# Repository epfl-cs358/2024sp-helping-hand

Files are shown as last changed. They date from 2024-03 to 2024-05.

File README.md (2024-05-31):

# Helping Hand

**Beyond Accessibility: Unleashing the Potential of Home Automation to Foster Independence and Inclusivity for Individuals with Unique Needs**

2024 - EPFL (CS-358) MIT - Group project



## Project's Overview

Helping Hand is an innovative project designed to enhance the independence of individuals with **mobility impairments** through adaptable **home automation**.
The core of the project is a **modular box** equipped with a **Wi-Fi** enabled microcontroller and a plotter like mechanism that allows **remote control** of various **household appliances**.
This system can be operated via a **smartphone or WEB application**, making it accessible for users with limited physical capabilities.

Inspired by the needs of Sean, a person with ALS who has limited mobility, Helping Hand aims to facilitate tasks such as opening doors and operating blinds without assistance.
The modular box can accommodate different remote controls, allowing users to control multiple devices through a single, user-friendly interface.
The project prioritizes accessibility, ease of use, and adaptability, making it a versatile solution for various remote-controlled appliances.

**Note**: you can check out the original project's proposal: [Helping Hand project proposal](proposal/out/proposal.pdf).

## Project's Structure

Below is a brief explanation of this repository's structure to provide context and aid readers' comprehension in the following sections of this document.

- `code` directory: contains all the code for the different parts of the project.
    - `CVserver`: the python server side program responsible for image processing and remote buttons automatic detection and configuration.
    - `esp32-cam`: the ESP-32 Cam [Arduino](https://www.arduino.cc/) code to be able to capture an image using an HTTP request.
    - `esp32-controller`: the ESP-32 C6 code that is responsible to control the motors and press the remote's buttons on the main plate.
    - `helping_hand`: the [Flutter](https://flutter.dev/) code used to create the application from which we control the device and interact with the different microcontrollers in the system.
- `design` directory: contains all the 3D modeling files and exports along with the laser cut sheets.
- `diagrams` directory: contains all the protocol diagrams specifying how the different parts of the system interact with one another.
- `documentation` directory: contains all the pictures and schematics to be able to reproduce this project.
- `proposal` directory: the [LaTeX](https://www.latex-project.org/) document used to write the original project proposal.
- `reports` directory: our first meetings reports to agree on what to do together.

## Build It Yourself !

This section is all about providing instructions and material to be able for anyone to reproduce this project by themselves.

### Hardware

This project is mainly composed of electronic components, laser cut _4mm_ MDF plates and 3D printed parts.

#### Main body

Here are the steps to follow to build the main body (and the camera module) of the system:

1. Laser cut the following MDF (4mm) parts
    - [Plotter](design/plotter/plotter.dxf)
    - [Cam holder](design/camholder.dxf)
2. 3D print the required parts (PETG)
    - [Gear holders for the column: top](design/plotter/plotter_column_2_belt_holder_top.stl)
    - [Gear holders for the column: bottom](design/plotter/plotter_column_2_belt_holder_bottom.stl) 
    - [All clamp parts](design/clamp/)
    - [All y axis parts](design/y_axis/)
3. For the assembly you will also need the following parts:
    - One _8mm_ diameter stainless steel bar, _290mm_ of length
    - One _8mm_ diameter stainless steel bar, _305mm_ of length
    - Two _8mm_ diameter stainless steel bar, _160mm_ of length
    - Four _8mm_ rod bearings to slide on the bars
    - Two _5mm_ diameter stainless steel bars, _150mm_ of length
    - Four _M4_ screws with nuts (two are nylon insert lock nuts), _35mm_ of length
    - Four _M4_ screws with nuts, _12mm_ of length
    - Eight _M3_ screws with nuts, _10mm_ of length
    - One _M5_ screw with nut, _20mm_ of length
    - Two _M5_ screws with nuts and spacers, _20mm_ of length
    - Eight _M3_ screws, _12mm_ of length
    - Two _M2.5_ screws with nuts, _12mm_ of length
    - Eight neodymium magnets, cubes of _5mm_ sides
    - Two rubber sheets, _30mm_ by _12mm_
    - Two plastic belts, _610mm_ and _320mm_
    - End gears and axes for the connection between belt and motors
4. Assemble everything and glue the MDF parts as indicated in the 3D step file: [Full assembly .step file](design/assembly.step).

For reference, here are some pictures of the full result assembly:

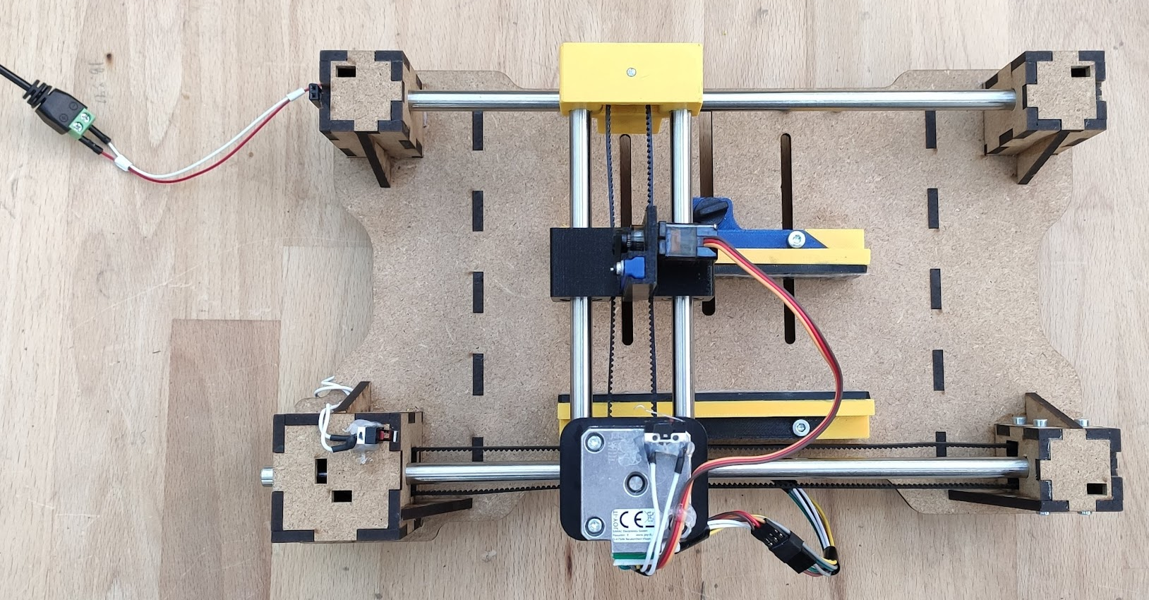
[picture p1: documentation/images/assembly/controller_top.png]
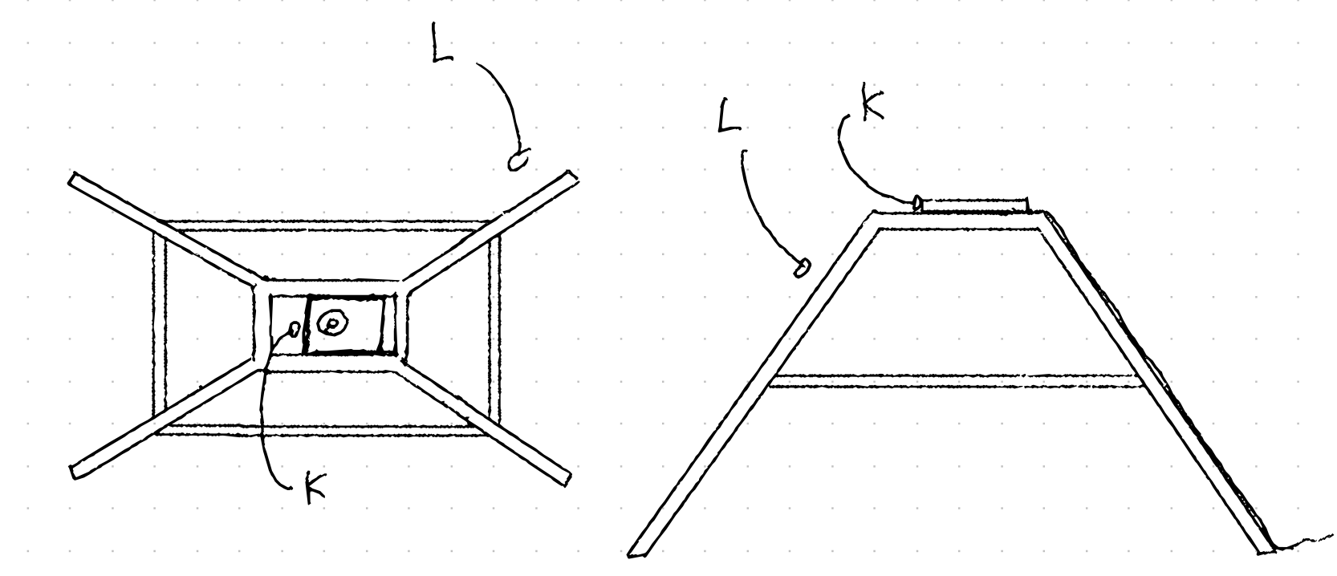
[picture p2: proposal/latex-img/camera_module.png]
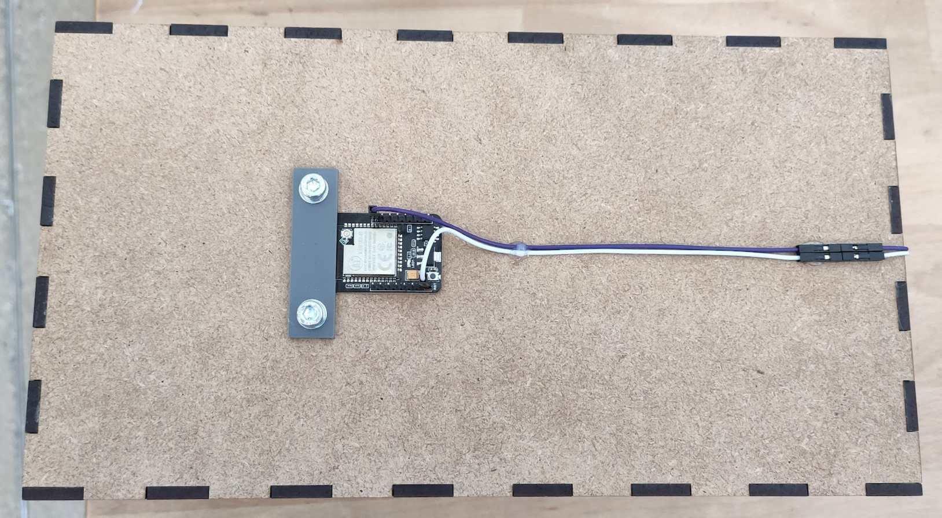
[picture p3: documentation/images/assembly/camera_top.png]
      

#### Electronics

Here are all the required electronic components:

- ESP-32 CAM
- ESP-32 C6
- Stepper mottors Nema14-01 (2 times)
- Motors drivers A4988 (2 times)
- Servo motor MG90S
- DC to DC converters (2 times)
- Two limit switches
- Condensator _100uF_ (2 times)
- Power Supply 9V

Wire everything together as indicated in the following schematic:

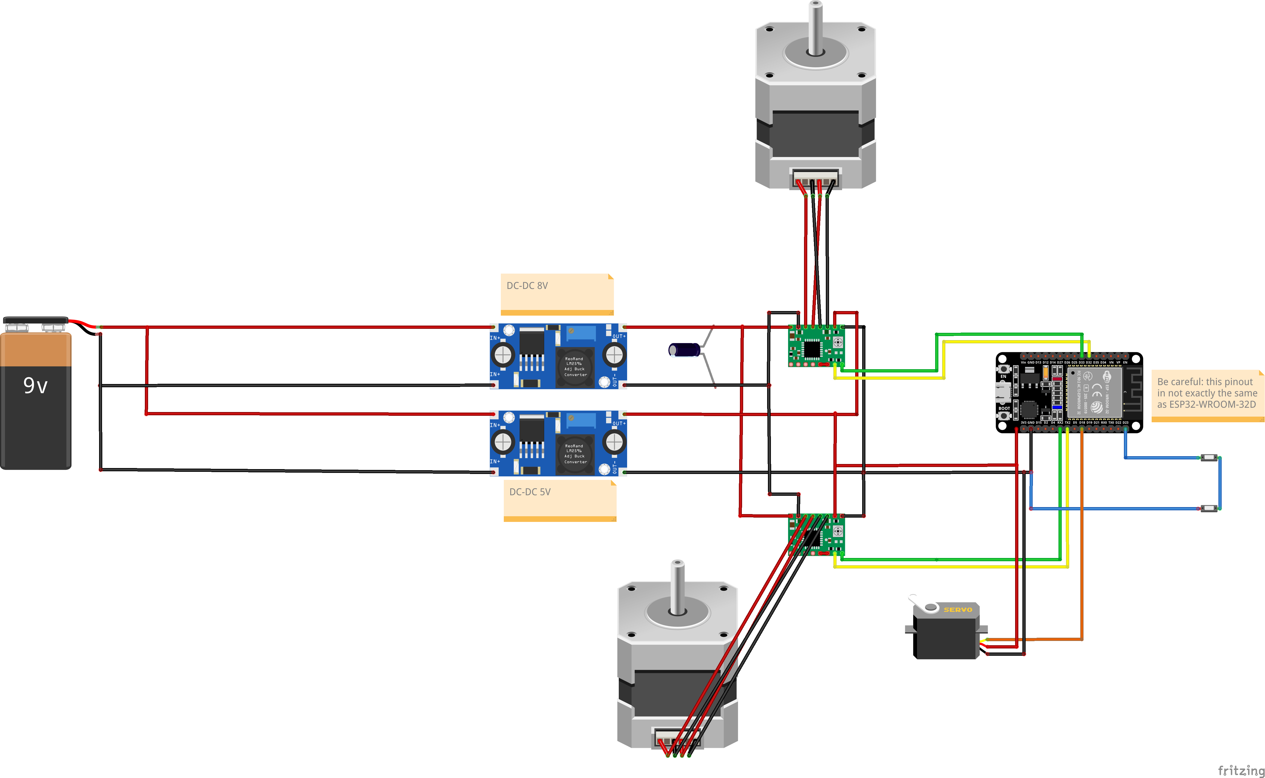
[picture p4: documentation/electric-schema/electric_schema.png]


**Note**: make sure to leave some length on the cables used on the travelling parts.

For reference, here are some pictures of the resulting cable management (done under the board):

<br>


### Software

We have four system components that need to interact with eachother in order to function properly.
The following diagram summarizes the different intractions between the components:

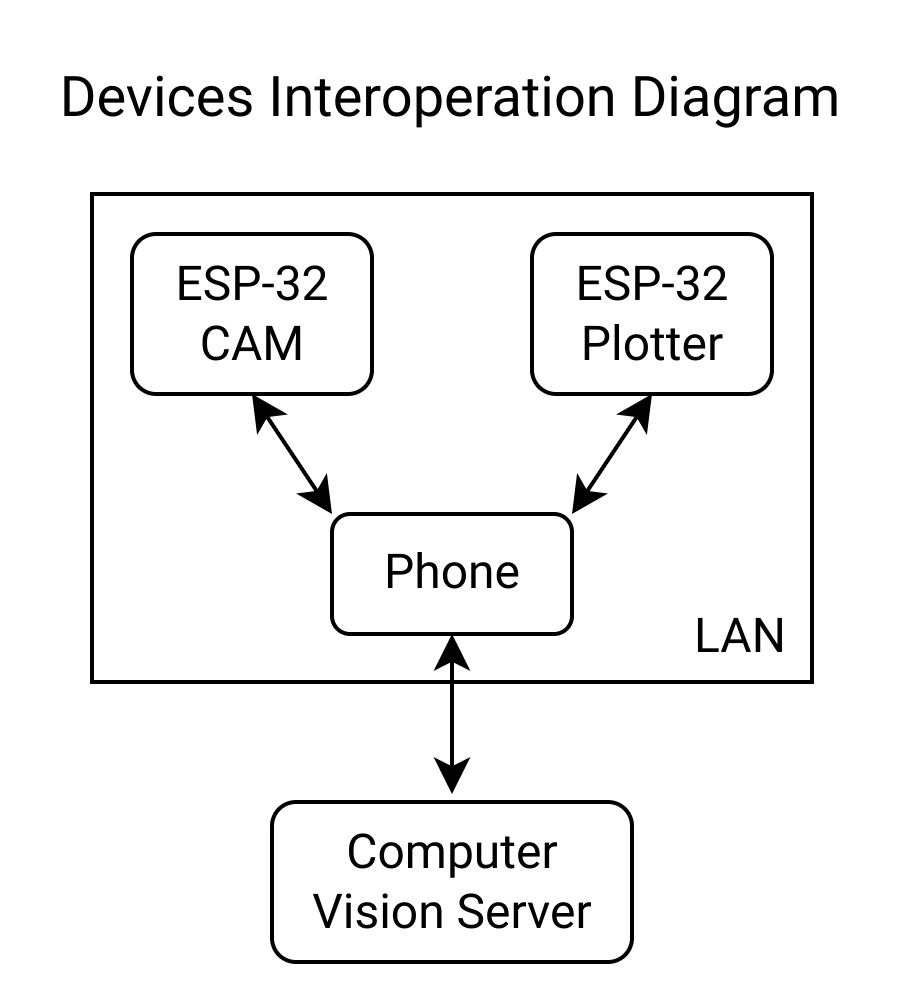
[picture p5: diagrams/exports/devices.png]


#### Application

All the system is driven by a [Flutter](https://flutter.dev/) cross-platform application.

You can install the Flutter dev environment by following the installation instructions (on any OS): https://docs.flutter.dev/get-started/install.

Then navigate to the directory of the application, `code/helping_hand`.
You can now launch the application on your platform of choice, on web for example `flutter run -d chrome`.
To build for other targets, you can follow the standard Flutter building procedures: https://docs.flutter.dev/deployment.

Here are a few pictures of the application interface:

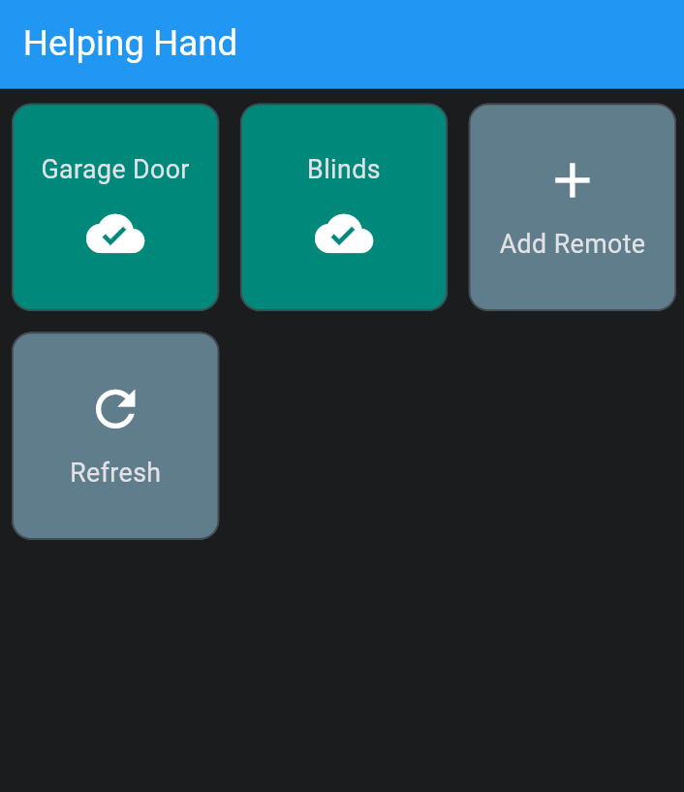
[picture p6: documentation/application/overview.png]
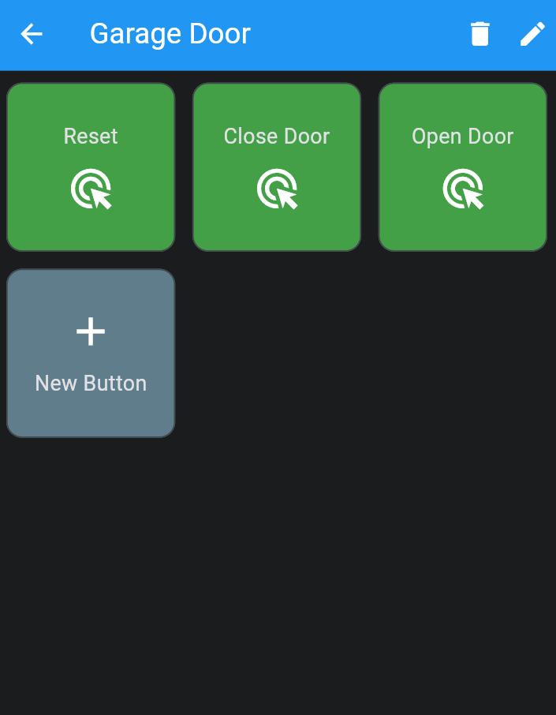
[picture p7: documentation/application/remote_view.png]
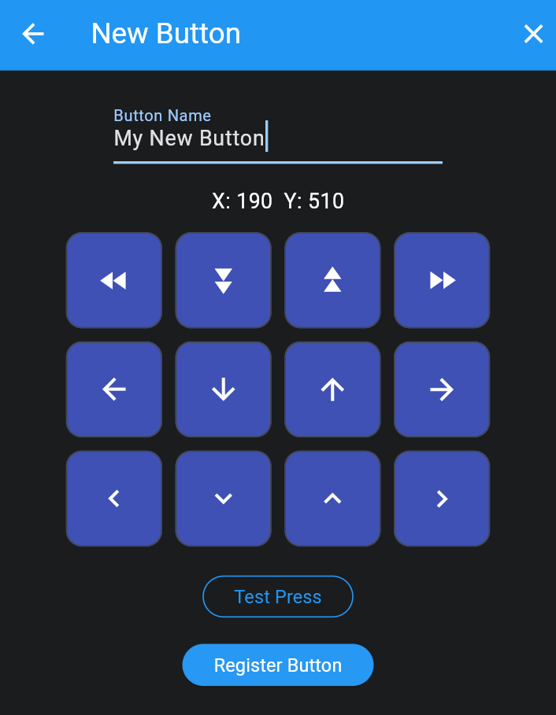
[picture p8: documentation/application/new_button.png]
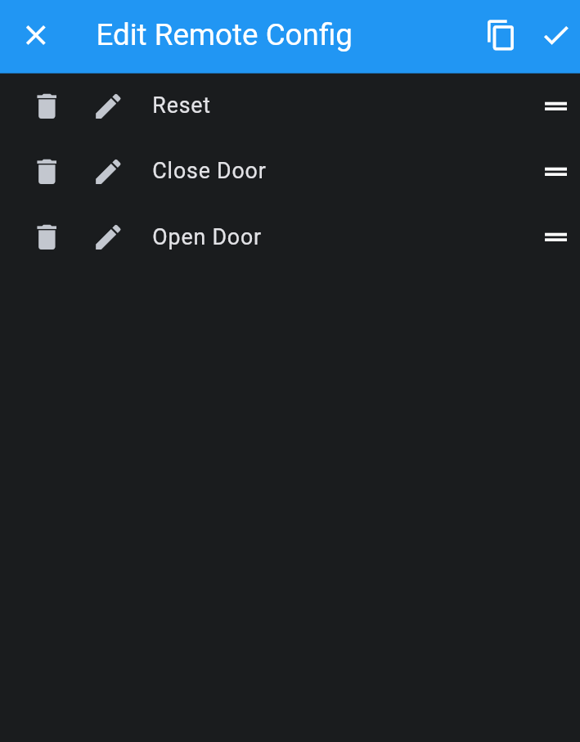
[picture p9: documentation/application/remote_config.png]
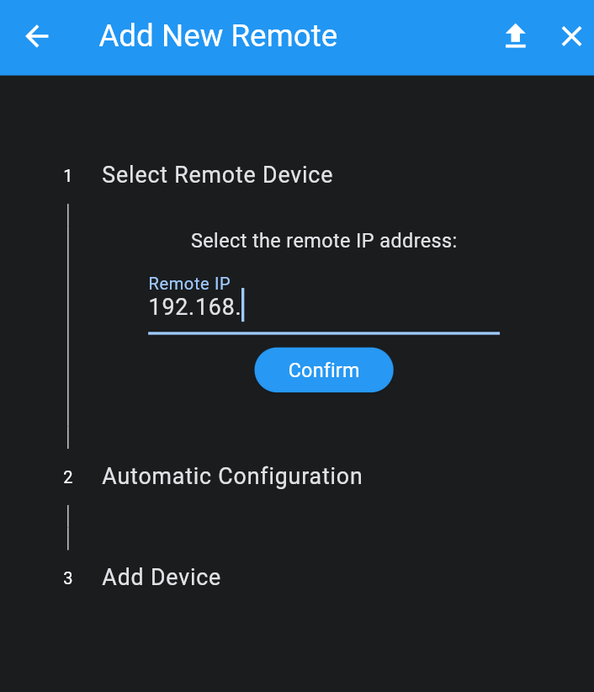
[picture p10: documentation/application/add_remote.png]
    

#### Arduino

We use the [Arduino IDE](https://www.arduino.cc/en/software) to flash the two ESP-32 boards:

- **ESP-32 Cam** (the automatic configuration module using the camera): flash the `code/esp32-cam/esp32-cam.ino`. For more information about this module, please refer to the [ESP-32 CAM README](code/esp32-cam/README.md).
- **ESP-32 Plotter** (the remote controller): flash the `code/esp32-controller/sketch_webServer/sketch_webServer.ino`. For more information about this module, please refer to the [ESP-32 C6 README](code/esp32-controller/README.md).

#### Computer Vision Server

We used a [Python](https://www.python.org/) web server (running on any computer or in the cloud) powered by the [Flask](https://flask.palletsprojects.com/en/3.0.x/) framework.

Refer to the associated README to setup the python server: [Python CVserver Setup README](code/CVserver/README.md).

## Contributors

- Yoan Giovannini ([@unglazedstamp](https://github.com/unglazedstamp))
- Nour Guermazi ([@nourguermazi](https://github.com/nourguermazi))
- Lucas Jung ([@gruvw](https://github.com/gruvw))
- Pinar Oray ([@pinar-oray](https://github.com/pinar-oray))
- Jonas Sulzer ([@violoncelloCH](https://github.com/violoncelloCH))

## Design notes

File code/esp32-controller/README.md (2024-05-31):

# Motor controller software
This folder contains the code running on the ESP-32-C6 which controls the motors.

## Setup to work with the ESP32-C6

### Arduino IDE
You first have to flash the sketch_initMemory.ino with your wifi credentials in the code (only the first time), then you can flash the sketch_webServer.ino code which will connect to the wifi to control the motors.

At the beginning of the file you will find all the constants needed to change the behavior of the helping-hand: the motors max speed, calibration speed, the pins number on the board and others.

### Wiring
wiring schema of the ESP32-C6
Connect all the wiring according the the schema and then adjust the pins to your ESP board and in the program.

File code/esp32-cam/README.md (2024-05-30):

# Camera module software
> This folder contains the code running on the camera module, an ESP32-CAM module. It has `/capture` endpoint serving an image of the remote.

## Setup to work with the ESP32-CAM

### Arduino IDE
> To work with this existing project, open the esp32-cam.ino file with Arduino IDE.

1. In `File>Preferences` in the field `Additional boards manager URLs` add the following two lines:
```
https://arduino.esp8266.com/stable/package_esp8266com_index.json
https://raw.githubusercontent.com/espressif/arduino-esp32/gh-pages/package_esp32_index.json
```
2. In `Tools>Board>Boards Manager` install the `esp32` package.
3. In `Tools>Board>esp32` select `AI Thinker ESP32-CAM`
4. For the Serial connection, set the baud to `115200` (dropdown at the top right of the serial console).

#### Setting the WIFI credentials
The WIFI credentials (SSID and Password) are set in the main Arduino project file: `esp32-cam.ino`. At the top of the file (line ~35) the credentials have to be set in the following lines:
```
// ===========================
// Enter your WiFi credentials
// ===========================
const char* ssid = "wifi-ssid";
const char* password = "wifi-password";
```

#### Flashing
`GND` and `IO0` need to be connected while powering on the ESP for it to boot in flashable mode. Use a cable to connect them. To boot the flashed program, remove the cable and reboot (i.e. power cycle) the ESP with the two pins not connected.

### Wiring
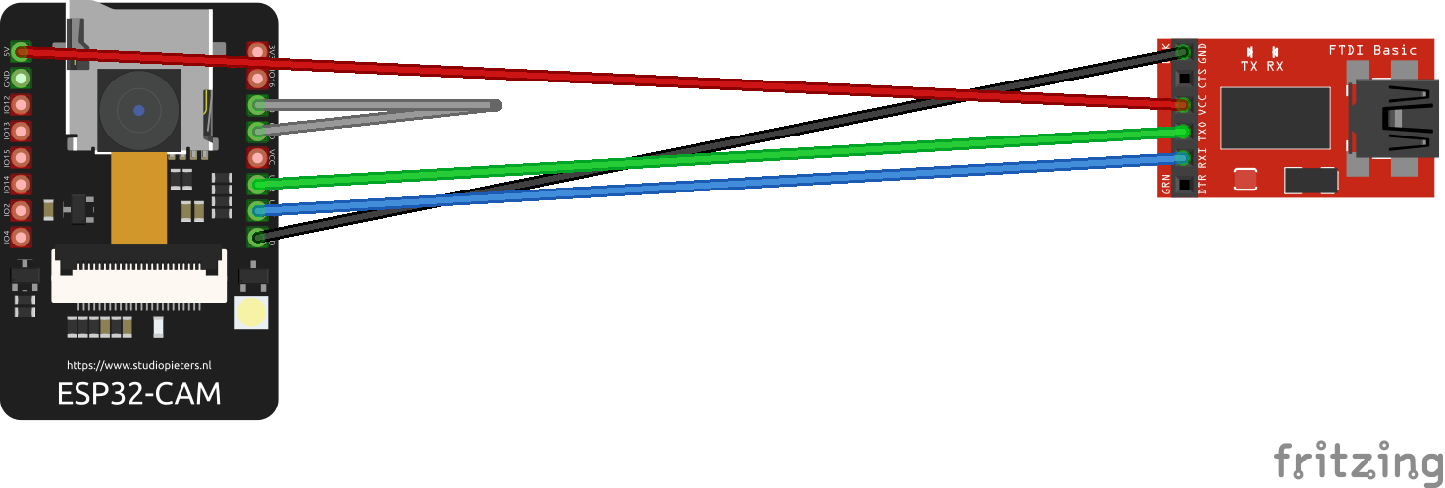
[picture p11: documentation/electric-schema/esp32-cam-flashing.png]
wiring schema for flashing

as described in the Course Handbook in Chapter 25.4  
note the two pins that need to be bridged (only) during flashing

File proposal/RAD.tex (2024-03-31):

\section{Risk Assessment}

In this section, we conduct a comprehensive risk assessment to identify potential challenges and vulnerabilities that could impede the success of our project.
By evaluating technological risks we aim to proactively address these issues through strategic planning and prototype development.
This assessment underscores our commitment to ensure the resilience and adaptability of our project, thereby minimizing the likelihood of failure and maximizing its overall effectiveness.

% reword the below p
%  remote adaptability: required pressure for each remote is different: some hard-pressed, some don't require as much pressure to acknowledge a button press. another problem is that the remote sizes
%                         vary a lot in length but especially in width, which makes designing and creating a clamp that fixes most of the remotes difficult.  
%  calibration: the calibration as a first step is to be done manually, which would include manually moving the pushing mechanism to the button via the phone application and setting it up as a button. This might be somewhat 
%                 time consuming and hard to configure for non-technical users. 
%                 The next step to the setup includes computer vision.
%                 This also comes with its own challenges, and is complex because of the camera quality of the ESP32-CAM, the nature of remotes and the setup restrictions: small and non-tv remotes are likely to have similar colored buttons to 
%                 the remote's main body, and this makes recognition of individual buttons difficult. Another issue is that the setup, i.e. placing the remote in the clamp is done by a person, and this causes reliability issues
%                 in the sense that not everyone can place and clamp the remote perfectly, and this will cause a sligtly different placement each time. This will cause in a different lightning and a different angle of view for
%                 the camera to pick up. This might affect the accuracy of the image recognition. The computer vision part requires an external computer to set up button positions, and this information is then
%                 sent to the phone application, Here, the communication between the computer, the phone app and the plotter is crucial and complicated. 

\begin{itemize}
    \item Power supplies to steppers:\\
        As mentioned in the manual, inadequate wiring practices and carelessness may lead to frying a computer or damaging the parts, especially the motor drivers and the stepper motors, potentially putting at risk the functionality of the project.
    \item Control of the solenoid:\\
        While the solenoid allows for a completely vertical and uni-directional movement, since we don't have experience with them, we're not sure how precisely we can control the acceleration and force of the resulting movement.
        An alternative could be to use a stepper motor instead for pressing the remote buttons.\\
        An additional risk could be that not all buttons require the same pressure. It could be difficult to adapt to this.
    \item Adaptability to different remotes:\\
        The project's adaptability to different remote controls is a challenge, as compatibility issues may arise with various types of remotes due to the vast spectrum of sizes. The amount of different size and shapes possible makes it complicated to design the clamp mechanism. 
    \item Magnet interferences:\\
        The presence of magnets in the project could disrupt the operation of sensitive electronic components such as the solenoid push-down mechanism, motors or the WiFi chip of the ESP32, leading to unpredictable behavior.
    \item WiFi network stability:\\
        The reliance on WiFi connectivity on those ESP32 microcontrollers introduces a risk related to network instability, which could affect communication between project components.
    \item Ease of configuration:\\
        The configuration and calibration of the plotter will have the possibility to be done in two ways: manually via the phone app or with computer vision via a computer. The manual setup may be time consuming for remotes with many buttons. 
        The camera and computer vision setup may be hard to configure for non-technical users. This option also has its own additional challenges. The recogni̇ti̇on of the remote and its buttons rely on the camera, the placement of the remote, the lightning of the room
        and overall restrictions due to remote design. These may affect the accuracy of the image recognition.
    \item Computer vision to button press precision:\\
        Detecting the correct position and therefore being able to guarantee a precise button press while using computer vision to calibrate and configure the device could be difficult for the same reasons listed in above point.
\end{itemize}

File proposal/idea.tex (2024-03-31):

\begin{minipage}[t]{0.65\textwidth}
    In the depicted image, you'll find Sean and Lucas.
    Sean, a colleague of Lucas' mother, is unfortunately grappling with \href{https://en.wikipedia.org/wiki/ALS}{amyotrophic lateral sclerosis}\footnotemark (ALS), a terminal neurodegenerative disease that progressively diminishes his mobility.
    Presently, he has to spend his days in an electric wheelchair, with only partial movement in his wrists.
    As a result, he relies on others for even the most basic tasks, such as opening a door or operating the lights in his home.
    Despite these challenges, Sean can still manage his smartphone while in his chair, thanks to a specialized joystick and a button.
    The objective of this project is to develop an adaptable solution that empowers people in a similar situation to regain some independence through the use of certain appliances in their home.
\end{minipage}\hfill
\begin{minipage}[t]{0.30\textwidth}
  \centering\raisebox{\dimexpr \topskip-\height}{
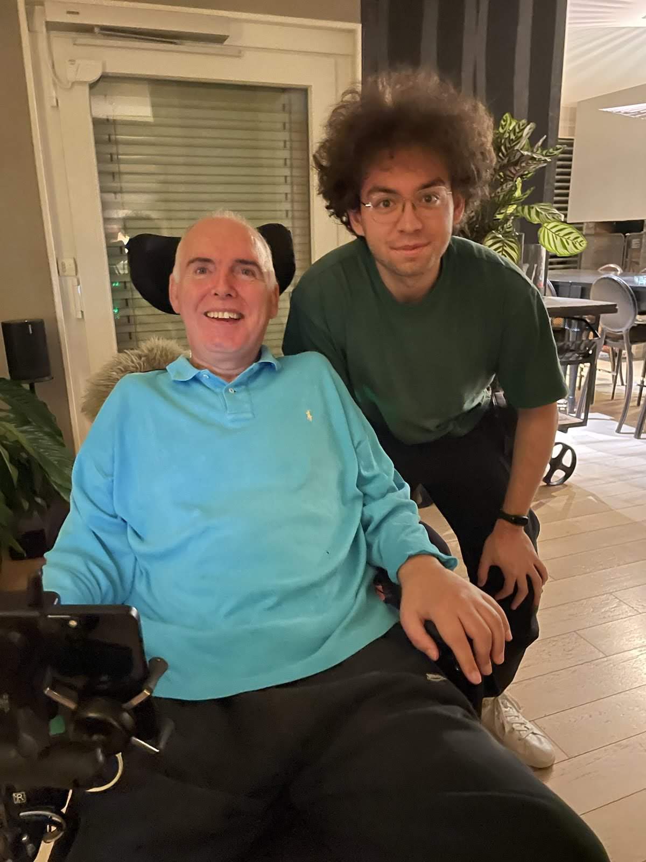
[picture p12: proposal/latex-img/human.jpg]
  }
\end{minipage}
\footnotetext{Amyotrophic Lateral Sclerosis: \url{https://en.wikipedia.org/wiki/ALS}}

\vspace{-10pt}

\section{High-level description}

The project aims to create a box in which the user can install any one of the various remote controls they have in their home.
The box will be equipped with a \footlink{plotter}{https://en.wikipedia.org/wiki/Plotter} like mechanism and a Wi-Fi capable microcontroller, allowing for remote operation of the enclosed remote control by having a solenoid activator attached to the plotter press on the buttons.
The box must be designed in such a way that the buttons are still usable without causing disruption to a user who prefers direct manual control of the remote.
The design of the case should also be easily adaptable to different type of remote controls.

Even though in the scope of the project we'll only be able to build one box, the idea is that a user can install multiple of these boxes for as many remotes as they want to use.
Each box is connected to the Wi-Fi network of the home it is installed in, and the user can command it by using an application on their smartphone.
Naturally, the application will be meticulously designed to maximize \footlink{accessibility}{https://en.wikipedia.org/wiki/Accessibility} for users with limited input capabilities.
Collaborative feedback and discussions with Sean will play a pivotal role in enhancing the system's accessibility, as he provides valuable insights from the perspective of a user with disabilities.

This project idea will be applied to some of the remote controlled appliances in Sean's home, notably in the two following use cases:
\begin{enumerate}
    \item In his residence, Sean has installed a motorized door (as seen behind us on the picture) that can be operated with a button press using a dedicated remote control, on which we could install the system.
        This holds significant importance for the project, as it would enable Sean to independently access his terrace and garden without relying on someone else to open the door for him.
    \item Additionally, he possesses remote-controlled blinds that he wishes to manage through his smartphone.
        This functionality would empower him to effortlessly close the blinds while working on his computer when the sun begins to shine through his window, or before going to bed.
\end{enumerate}

This project maintains its independence from specific use cases at Sean's place, aiming to be easily adaptable to most remote controls.
Nevertheless, establishing a direct connection and receiving periodic feedback from an end user like Sean during development significantly contributes to ensuring the system's accuracy and user-friendliness directly from the targeted audience.

Furthermore, the potential extends beyond Sean's specific needs: this system could serve as a prototype or a \footlink{minimal viable product}{https://en.wikipedia.org/wiki/Minimum_viable_product} (MVP)/pilot experiment for a cost-effective and easy to install commercial solution for a future startup company.
Such a solution would offer increased autonomy to numerous individuals in their daily lives.
It would be particularly competitive compared to existing alternatives that are very costly and often necessitate replacing the entire system with a ``smart``/digital version even though the one currently in place still works properly.
In fact, even though this system is targeted at people with disabilities, it might also come in handy for everyone who wishes to have access to their regular appliances through a common, digitalized interface.

A fundamental aspect of this project is its commitment to adhering to \footlink{open standards}{https://en.wikipedia.org/wiki/Open_standard} and the \footlink{open source}{https://en.wikipedia.org/wiki/Open_source} philosophy.
This commitment ensures the system's ease of customization for anyone interested in enhancing, tweaking, or adding functionalities.
This stands in stark contrast to existing solutions in the market, which are often characterized by closed systems that are challenging or even impossible to integrate into a accessible and simple to use central app and lack customization options.

\subsection{User Stories}

\begin{itemize}
    \item As a user with limited mobility, I want to independently open and close my motorized door using my smartphone, so I can access my terrace and garden without assistance.
    \item As a user who values autonomy, I want the modular box to be connected to the Wi-Fi network in my home, allowing me to control appliances remotely through my smartphone from anywhere in the house.
    \item As a user with a chronic degenerative disease affecting my mobility, I want to control my remote-controlled blinds via a smartphone app, allowing me to manage sunlight in my room without relying on others.
    \item As a user with unique needs, I want the modular box to be adaptable to different types of remote controls in my home, ensuring flexibility in controlling various appliances.
    \item As a potential end user looking for cost-effective solutions, I am looking for a commercial solution that offers increased autonomy, making it a viable and affordable option for individuals with diverse needs.
    \item As a developer or tech enthusiast, I want the system to adhere to open standards and open source philosophy, enabling me to enhance, customize, or add functionalities by making \footlink{pull requests}{https://en.wikipedia.org/wiki/Distributed_version_control} to the project's repository.
    \item As a user assisting someone with unique needs, I want the setup of the box and the configuration of the app to be straightforward and require minimal technical expertise, ensuring that I can provide support without complications even if I am not very skilled with new technologies.
    \item As a user with limited physical dexterity, I want to operate my TV remote control from my smartphone using the modular box system, allowing me to enjoy television without struggling with a conventional remote control.
\end{itemize}

\subsection{Existing Projects}

After searching online for existing solutions, Lucas discovered that none fully align with the objectives outlined above.
Many of the identified projects focus on complete replacement of the remote control, utilizing new emitters controlled by a microcontroller.
These implementations typically involve either \footlink{infrared emitters (project)}{https://github.com/computerjazz/ir-mobile} that record signals from the targeted remote control or \footlink{radio frequency (project)}{https://github.com/loopj/open-rts} based emitters that analyze the \footlink{rolling codes}{https://en.wikipedia.org/wiki/Rolling_code} of the initial device.

While these approaches are great and offer reliable performance, they are not well-suited for the inclusive and versatile goals of this project.
They often require installation on specific hardware and involve intricate setup and code manipulation to function.
This project aims to take a more broad and user-friendly approach by designing an adaptive solution that seamlessly integrates with various remote controls out of the box, whatever transmission mechanism they might use.

\section{Technical Specifications}

\textbf{Hardware Components}

The core of the modular box will utilize the \footlink{ESP32}{https://www.espressif.com/sites/default/files/documentation/esp32_datasheet_en.pdf} microcontroller for its compact size, low power consumption, and Wi-Fi capabilities.
This will enable seamless communication with the home network and the user's smartphone application.
Each box will be equipped with one ESP32 that will host and expose a \footlink{Web API}{https://en.wikipedia.org/wiki/Web_API} to interact with the plotter stepper motors and solenoid actuator from the smartphone application via the home Wi-Fi network.

The remote control will be housed in a laser-cut adjustable wood case/holding to accommodate various sizes and shapes.
The design should prioritize accessibility, ensuring that buttons remain accessible for direct manual control when needed.

Equipped with a plotter-like system, the box will simulate human interaction with the enclosed remote control.
This plotter system enables precise and controlled button presses, ensuring reliable functionality by moving to the exact position of the button and then actuating the button through a purely vertical movement done by the solenoid.

In a basic configuration process, after installing the remote in the box, the user selects button position by manually positioning the plotter using arrow buttons in the app.
The coordinate of that position is then saved and associated with a button and label in the app.

Additionally, to facilitate the setup process, an attachable module with a camera allows to assist the configuration of the device through computer vision.
If a user has multiple boxes in their home, they can use that single camera module to configure all of the boxes since it's only used during the setup process.
The computer vision, running on an external computer, also communicates over the network with the ESP32 board as well as with the camera to get the video feed.
The software detects the buttons on the image of the remote and allows the user to select the buttons to make available through the app.
For each of the chosen buttons, it auto-detects the exact position to execute the button press operation thanks to the visual feedback provided by the camera.
In case the user prefers not to use the camera and computer vision or in case the computer vision fails due to low contrast or a special remote type/design the manual setup process serves as a fallback. 

\begin{minipage}[t]{0.45\textwidth}
    \centering\raisebox{\dimexpr \topskip-\height}{
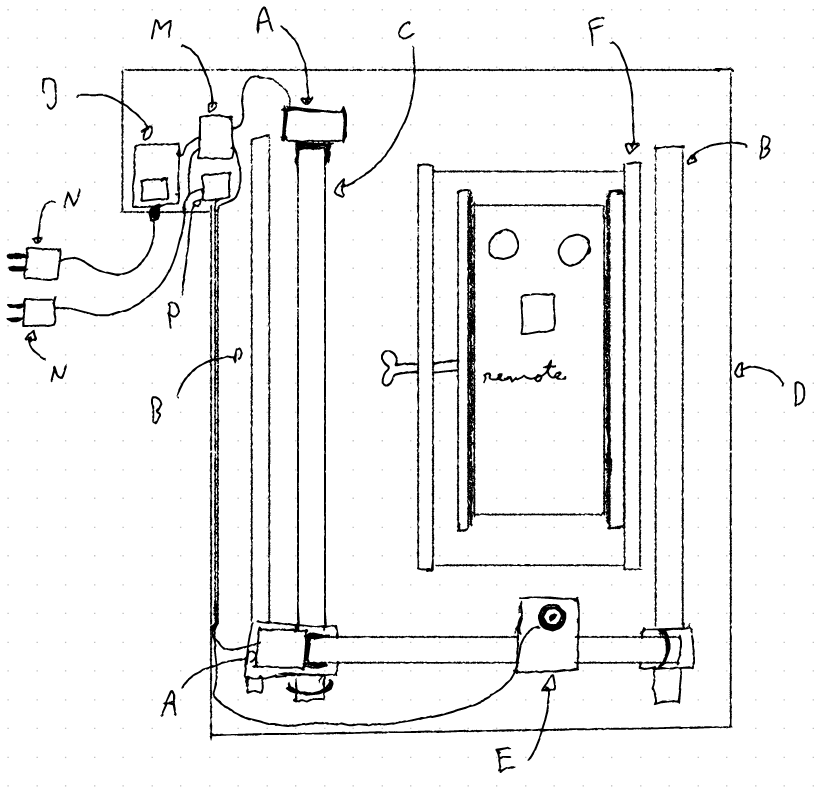
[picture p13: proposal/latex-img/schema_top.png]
    }
\end{minipage}\hfill
\begin{minipage}[t]{0.5\textwidth}
    Looking from the top, we can see the base plate with the different components on it.\\

    Legend:
    \begin{itemize}
        \item (A) motors
        \item (B) rail (metal rod)
        \item (C) lead screw
        \item (D) base plate
        \item (E) solenoid holder
        \item (F) clamp
        \item (G) solenoid
        \item (H) wingnut
        \item (I) rubber
        \item (J) ESP32-c6
    \end{itemize}
\end{minipage}

\begin{minipage}[t]{0.5\textwidth}
    \begin{itemize}
        \item (K) ESP32-CAM
        \item (L) camera module
        \item (M) motor controller
        \item (N) power supply
        \item (P) solenoid controller
    \end{itemize}
    \vspace{5mm}

    From the side we can see how the plotter can move on the two axis hovering above the remote.
\end{minipage}
\begin{minipage}[t]{0.45\textwidth}
    \centering\raisebox{\dimexpr \topskip-\height}{
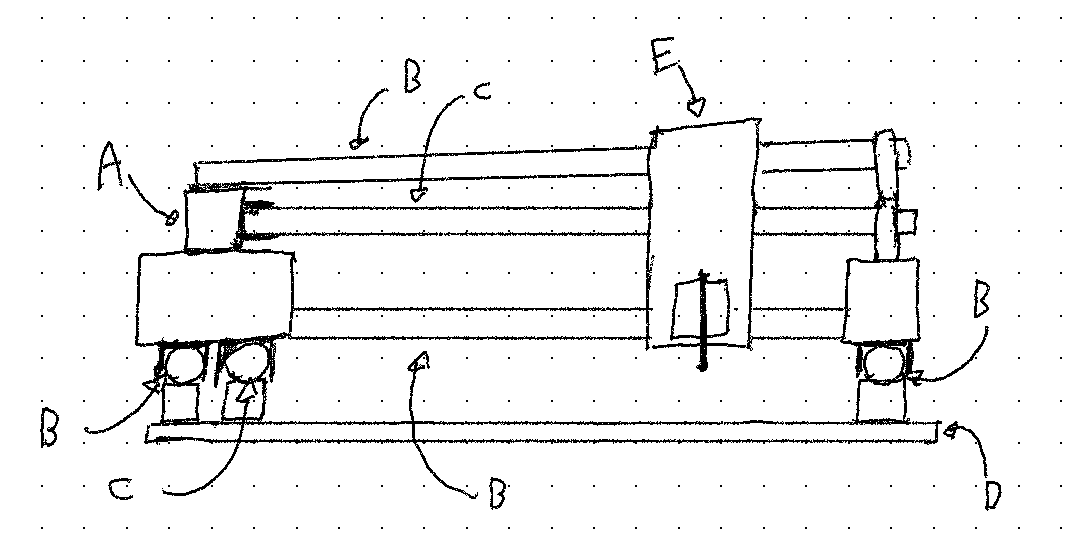
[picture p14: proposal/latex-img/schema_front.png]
    }
\end{minipage}\hfill

\begin{minipage}[t]{0.45\textwidth}
    \centering\raisebox{\dimexpr \topskip-\height}{
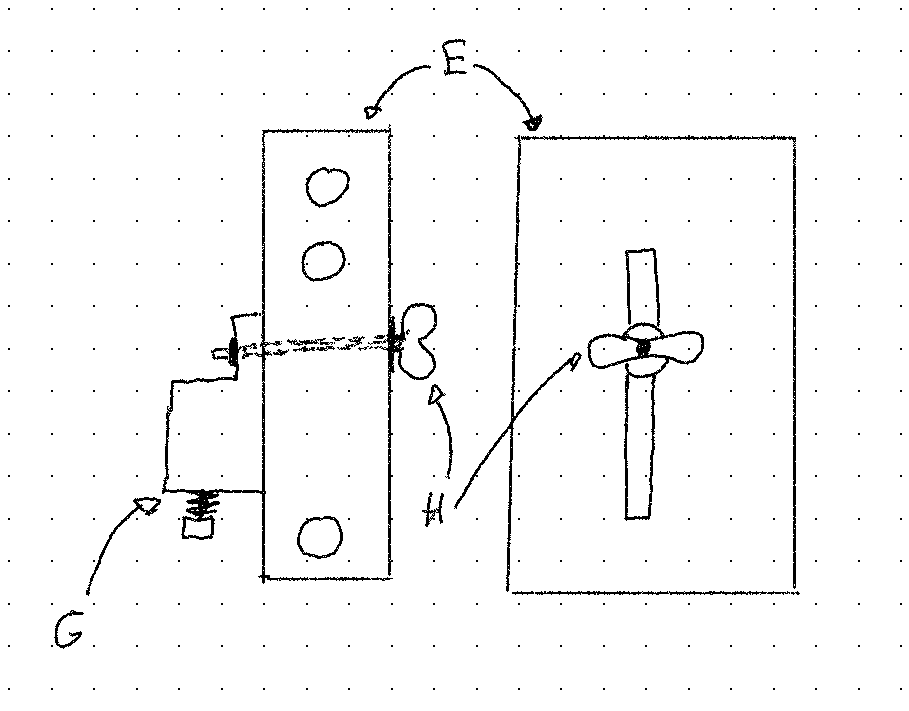
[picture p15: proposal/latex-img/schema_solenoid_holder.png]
    }
\end{minipage}\hfill
\begin{minipage}[t]{0.5\textwidth}
    \vspace{5mm}
    In the detail view of the solenoid holder we can see how the height of the solenoid can be adjusted to match the thickness of the remote.
\end{minipage}

\begin{minipage}[t]{0.5\textwidth}
    \vspace{5mm}
    The clamp allows to safely hold the remote in place.
\end{minipage}
\begin{minipage}[t]{0.45\textwidth}
    \centering\raisebox{\dimexpr \topskip-\height}{
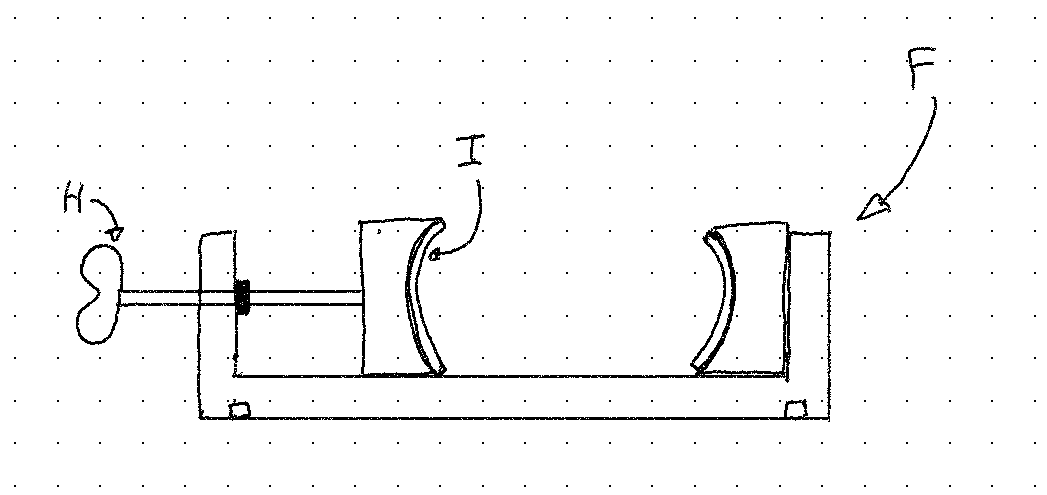
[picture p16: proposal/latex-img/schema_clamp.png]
    }
\end{minipage}\hfill

\begin{minipage}[t]{0.40\textwidth}
    \centering\raisebox{\dimexpr \topskip-\height}{
    }
\end{minipage}\hfill
\begin{minipage}[t]{0.5\textwidth}
    \vspace{5mm}
    And finally the camera module.
\end{minipage}

\textbf{Software}

The software side of the project will be implemented using \footlink{Arduino}{https://www.arduino.cc/} programming to control the ESP32 microcontroller.
Arduino's user-friendly environment allows for efficient development and rapid iteration.

The dedicated smartphone application will be developed using the \footlink{Flutter framework}{https://flutter.dev/}.
The application will prioritize accessibility, offering a user-friendly interface tailored to individuals with limited input capabilities.
It should allow easy control of multiple boxes installed in the house.

The computer vision part is running on a computer assisting the setup. 
The application on the computer tries to recognize buttons on the remote and allows to easily choose the ones that should be accessible in the smartphone app.
When a button is selected, the computer vision calibrates the position for the button press and allows to test whether a button press actually works.
Finally, the configuration can be transferred to the smartphone by temporarily storing it on the ESP32.

We also need to design and implement an automatic network discovery protocol in order to automatically detect available remotes.
As we want to support many remote encasings in a single home network, the protocol has to assure correct communication between all the ESP32 boards and the smartphone application.

If time permits, we could enhance the application by incorporating a built-in voice controlled feature.
This addition would empower users to effortlessly command various devices using their voice, providing a more seamless experience.

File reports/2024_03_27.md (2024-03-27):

# Refined proposal

## Needs to be covered during the meeting

- [ ] Reviewed the proposal, any remark ?
- [ ] Check for precise drawing and skteches
- [ ] Add drawings and descriptions to the proposal
- [ ] Change the RAD with more details
- [ ] Reviewed the final BOM

## Needs to be done before Friday evening

- [ ]

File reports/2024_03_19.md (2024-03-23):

# Refined proposal

## Needs to be covered during the meeting

- [X] Go through the proposal and change what we want
- [X] Add drawings/sketches/computer graphics to the proposal
- [X] Go through the BOM and check it is ok + check links + find missing materials
- [X] Go through the RAD and check it is ok
- [X] Create the work breakdown (backlog) GitHub project, add dependencies
- [X] Discuss any hardward/software addition that we could add if time allows
    - Make it small
    - Make it look beautiful

## To discuss with TAs

- [X] Servo motors
- [X] Ask about feedback and bring it home to try it out
- [X] Review design + magnet vs fit and clip + z axis ideas

- Add an IR sensor + replayer
- Make it small slick and like a product
- Very easy to configure

## What needs to be Done before next Meeting

- [ ] Drawings to include on proposal
- [ ] Add and comment sketches on the proposal
- [X] Improve RAD and BOM

- [X] Add other use casses to the proposal
- [ ] Everyone review and read the full proposal

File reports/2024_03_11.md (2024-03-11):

# First Meeting

2024_03_11 - RLC781

## Discussed during the meeting

- Setup and invite to common project repository on Github
- Setup meeting reports repository
- Setup latex report and compile using the Makefile
- Talked about the design
- Meetings on Tuesdays 8:30 AM till 9:30 AM

## BOM - Bill of Materials

- 10 servo mottors
- 4 esp8266 + 32
- Small neodium magnets
- Ask for rubber like material

## RAD - Risk Assesment Document

- Power supplies to servos
- Adaptability to different remotes
- Magnet interferences
- WiFi network stability
- How deep the motor goes
- Ease of configuration

## Next Meeting

- First write of BOM and RAD
- Feedback on revised proposal
- Split up work

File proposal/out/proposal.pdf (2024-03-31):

CS-358 MIT | Helping Hand

# Helping Hand

### Lucas Jung - IN BA6 324724 Nour Guermazi - SC BA6 314474 Pinar Oray - IN BA6 311543 Jonas Sulzer - IN BA6 325554 Yoan Giovannini - IN BA6 303934

2024 - 03

Beyond Accessibility: Unleashing the Potential of Home Automation to Foster Independence and Inclusivity for Individuals with Unique Needs

## Contents

1 High-level description | 2
2 Technical Specifications | 4
3 Bill of Materials | 7
4 Risk Assessment | 8

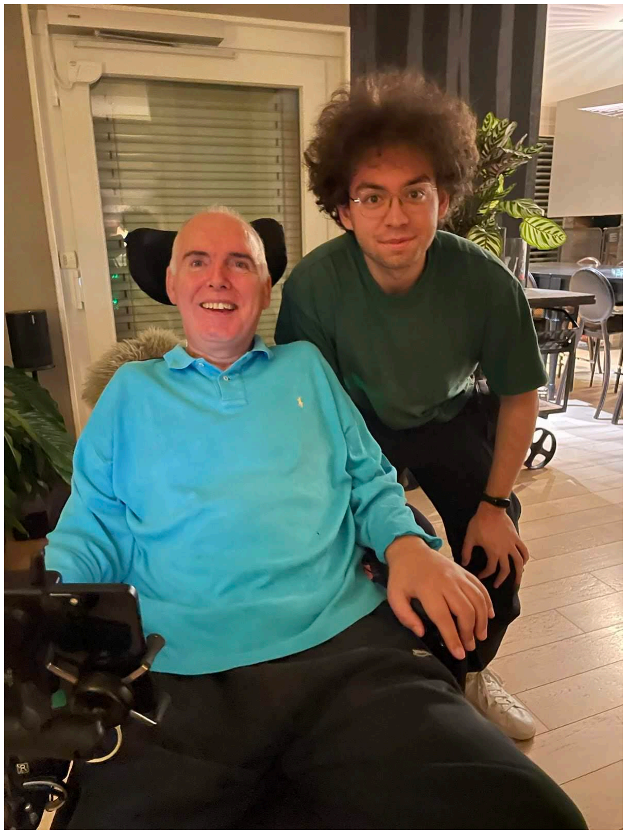
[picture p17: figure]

In the depicted image, you’ll find Sean and Lucas. Sean, a colleague of Lucas’ mother, is unfortunately grappling with amyotrophic lateral sclerosis¹ (https://en.wikipedia.org/wiki/ALS)
(ALS), a terminal neurodegenerative disease that progressively diminishes his mobility. Presently, he has to spend his days in an electric wheelchair, with only partial movement in his wrists. As a result, he relies on others for even the most basic tasks, such as opening a door or operating the lights in his home. Despite these challenges, Sean can still manage his smartphone while in his chair, thanks to a specialized joystick and a button. The objective of this project is to develop an adaptable solution that empowers people in a similar situation to regain some independence through the use of certain appliances in their home.

1Amyotrophic Lateral Sclerosis: https://en.wikipedia.org/wiki/ALS

## 1 High-level description

The project aims to create a box in which the user can install any one of the various remote controls they have in their home. The box will be equipped with a plotter² (https://en.wikipedia.org/wiki/Plotter)
like mechanism and
a Wi-Fi capable microcontroller, allowing for remote operation of the enclosed remote control by having a solenoid activator attached to the plotter press on the buttons. The box must be designed in such a way that the buttons are still usable without causing disruption to a user who prefers direct manual control of the remote. The design of the case should also be easily adaptable to different type of remote controls.

Even though in the scope of the project we’ll only be able to build one box, the idea is that a user can install multiple of these boxes for as many remotes as they want to use. Each box is connected to the Wi-Fi network of the home it is installed in, and the user can command it by using an application on their smartphone. Naturally, the application will be meticulously designed to maximize accessibility³ (https://en.wikipedia.org/wiki/Accessibility)
for users with limited input capabilities. Collaborative feedback and discussions with Sean will play a pivotal role in enhancing the system’s accessibility, as he provides valuable insights from the perspective of a user with disabilities.

This project idea will be applied to some of the remote controlled appliances in Sean’s home, notably in the two following use cases:

1. In his residence, Sean has installed a motorized door (as seen behind us on the picture) that can be operated with a button press using a dedicated remote control, on which we could install the system. This holds significant importance for the project, as it would enable Sean to independently access his terrace and garden without relying on someone else to open the door for him.
2. Additionally, he possesses remote-controlled blinds that he wishes to manage through his smartphone. This functionality would empower him to effortlessly close the blinds while working on his computer when the sun begins to shine through his window, or before going to bed.

This project maintains its independence from specific use cases at Sean’s place, aiming to be easily adaptable to most remote controls. Nevertheless, establishing a direct connection and receiving periodic feedback from an end user like Sean during development significantly contributes to ensuring the system’s accuracy and user-friendliness directly from the targeted audience.

Furthermore, the potential extends beyond Sean’s specific needs: this system could serve as a prototype or a minimal viable product⁴ (https://en.wikipedia.org/wiki/Minimum_viable_product)
(MVP)/pilot experiment for a cost-effective and easy to install commercial solution for a future startup company. Such a solution would offer increased autonomy to numerous individuals in their daily lives. It would be particularly competitive compared to existing alternatives that are very costly and often necessitate replacing the entire system with a “smart“/digital version even though the one currently in place still works properly. In fact, even though this system is targeted at people with disabilities, it might also come in handy for everyone who wishes to have access to their regular appliances through a common, digitalized interface.

A fundamental aspect of this project is its commitment to adhering to open standards⁵ (https://en.wikipedia.org/wiki/Open_standard) and

2Plotter: https://en.wikipedia.org/wiki/Plotter
3Accessibility: https://en.wikipedia.org/wiki/Accessibility
4Minimal viable product: https://en.wikipedia.org/wiki/Minimum_viable_product 5Open standards: https://en.wikipedia.org/wiki/Open_standard the open source⁶ (https://en.wikipedia.org/wiki/Open_source) philosophy. This commitment ensures the system’s ease of customization for anyone interested in enhancing, tweaking, or adding functionalities. This stands in stark contrast to existing solutions in the market, which are often characterized by closed systems that are challenging or even impossible to integrate into a accessible and simple to use central app and lack customization options.

### 1.1 User Stories

- As a user with limited mobility, I want to independently open and close my motorized door using my smartphone, so I can access my terrace and garden without assistance.
- As a user who values autonomy, I want the modular box to be connected to the Wi-Fi network in my home, allowing me to control appliances remotely through my smartphone from anywhere in the house.
- As a user with a chronic degenerative disease affecting my mobility, I want to control my remote-controlled blinds via a smartphone app, allowing me to manage sunlight in my room without relying on others.
- As a user with unique needs, I want the modular box to be adaptable to different types of remote controls in my home, ensuring flexibility in controlling various appliances.
- As a potential end user looking for cost-effective solutions, I am looking for a commercial solution that offers increased autonomy, making it a viable and affordable option for individuals with diverse needs.
- As a developer or tech enthusiast, I want the system to adhere to open standards and open source philosophy, enabling me to enhance, customize, or add functionalities by making pull requests⁷ (https://en.wikipedia.org/wiki/Distributed_version_control)
to the project’s repository.
- As a user assisting someone with unique needs, I want the setup of the box and the configuration of the app to be straightforward and require minimal technical expertise, ensuring that I can provide support without complications even if I am not very skilled with new technologies.
- As a user with limited physical dexterity, I want to operate my TV remote control from my smartphone using the modular box system, allowing me to enjoy television without struggling with a conventional remote control.

### 1.2 Existing Projects

After searching online for existing solutions, Lucas discovered that none fully align with the objectives outlined above. Many of the identified projects focus on complete replacement of the remote control, utilizing new emitters controlled by a microcontroller. These implementations typically involve either infrared emitters (project)⁸ (https://github.com/computerjazz/ir-mobile)
that record signals from the targeted remote control or radio frequency (project)⁹ (https://github.com/loopj/open-rts) based emitters that analyze the rolling codes¹⁰ (https://en.wikipedia.org/wiki/Rolling_code) of the initial device.

6Open source: https://en.wikipedia.org/wiki/Open_source
7Pull requests: https://en.wikipedia.org/wiki/Distributed_version_control

8
Infrared emitters (project): https://github.com/computerjazz/ir-mobile 9Radio frequency (project): https://github.com/loopj/open-rts
10Rolling codes: https://en.wikipedia.org/wiki/Rolling_code

While these approaches are great and offer reliable performance, they are not well-suited for the inclusive and versatile goals of this project. They often require installation on specific hardware and involve intricate setup and code manipulation to function. This project aims to take a more broad and user-friendly approach by designing an adaptive solution that seamlessly integrates with various remote controls out of the box, whatever transmission mechanism they might use.

## 2 Technical Specifications

Hardware Components

The core of the modular box will utilize the ESP32¹¹ (https://www.espressif.com/sites/default/files/documentation/esp32_datasheet_en.pdf) microcontroller for its compact size, low power consumption, and Wi-Fi capabilities. This will enable seamless communication with the home network and the user’s smartphone application. Each box will be equipped with one ESP32 that will host and expose a Web API¹² (https://en.wikipedia.org/wiki/Web_API) to interact with the plotter stepper motors and solenoid actuator from the smartphone application via the home Wi-Fi network.

The remote control will be housed in a laser-cut adjustable wood case/holding to accommodate various sizes and shapes. The design should prioritize accessibility, ensuring that buttons remain accessible for direct manual control when needed.

Equipped with a plotter-like system, the box will simulate human interaction with the enclosed remote control. This plotter system enables precise and controlled button presses, ensuring reliable functionality by moving to the exact position of the button and then actuating the button through a purely vertical movement done by the solenoid.

In a basic configuration process, after installing the remote in the box, the user selects button position by manually positioning the plotter using arrow buttons in the app. The coordinate of that position is then saved and associated with a button and label in the app.

Additionally, to facilitate the setup process, an attachable module with a camera allows to assist the configuration of the device through computer vision. If a user has multiple boxes in their home, they can use that single camera module to configure all of the boxes since it’s only used during the setup process. The computer vision, running on an external computer, also communicates over the network with the ESP32 board as well as with the camera to get the video feed. The software detects the buttons on the image of the remote and allows the user to select the buttons to make available through the app. For each of the chosen buttons, it auto-detects the exact position to execute the button press operation thanks to the visual feedback provided by the camera. In case the user prefers not to use the camera and computer vision or in case the computer vision fails due to low contrast or a special remote type/design the manual setup process serves as a fallback.

11ESP32: https://www.espressif.com/sites/default/files/documentation/esp32_datasheet_en.p df (https://www.espressif.com/sites/default/files/documentation/esp32_datasheet_en.pdf)
12Web API: https://en.wikipedia.org/wiki/Web_API

Looking from the top, we can see the base plate with the different components on it.

Legend:
- (A) motors
- (B) rail (metal rod)
- (C) lead screw
- (D) base plate
- (E) solenoid holder
- (F) clamp
- (G) solenoid
- (H) wingnut
- (I) rubber
- (J) ESP32-c6


- (K) ESP32-CAM
- (L) camera module
- (M) motor controller
- (N) power supply
- (P) solenoid controller

From the side we can see how the plotter can move on the two axis hovering above the remote.

In the detail view of the solenoid holder we can see how the height of the solenoid can be adjusted to match the thickness of the remote.


The clamp allows to safely hold the remote in place.


And finally the camera module.

Software

The software side of the project will be implemented using Arduino¹³ (https://www.arduino.cc/) programming to control the ESP32 microcontroller. Arduino’s user-friendly environment allows for efficient development and rapid iteration.

The dedicated smartphone application will be developed using the Flutter framework¹⁴. (https://flutter.dev/) The application will prioritize accessibility, offering a user-friendly interface tailored to individuals with limited input capabilities. It should allow easy control of multiple boxes installed in the house.

The computer vision part is running on a computer assisting the setup. The application on the computer tries to recognize buttons on the remote and allows to easily choose the ones that should be accessible in the smartphone app. When a button is selected, the computer vision calibrates the position for the button press and allows to test whether a button press actually works. Finally, the configuration can be transferred to the smartphone by temporarily storing it on the ESP32.

We also need to design and implement an automatic network discovery protocol in order to automatically detect available remotes. As we want to support many remote encasings in a single home network, the protocol has to assure correct communication between all the ESP32 boards and the smartphone application.

If time permits, we could enhance the application by incorporating a built-in voice controlled feature. This addition would empower users to effortlessly command various devices using their voice, providing a more seamless experience.

13Arduino: https://www.arduino.cc/14Flutter framework: https://flutter.dev/

## 3 Bill of Materials

The Bill of Materials (BOM) is a key part of our proposal, listing all required materials, quantities, specifications, and estimated costs. It streamlines procurement, budgeting, and decision-making, showcasing our meticulous planning and resource management.

- ESP32 C6 - 1 time - 12.95 CHF - https://www.conrad.ch/de/p/espressif-esp32-c6-devkitc-1-n8-entwicklungsboard-espressif-2992162.html (https://www.conrad.ch/de/p/espressif-esp32-c6-devkitc-1-n8-entwicklungsboard-espressif-2992162.html)
- ESP32 CAM - 1 time - 13 CHF - in stock
- NEMA 14 motors - 2 times - 17 CHF - https://www.conrad.ch/de/p/joy-it-schrit tmotor-nema14-01-neu-0-1-nm-0-4-a-wellen-durchmesser-5-mm-2142507.html (https://www.conrad.ch/de/p/joy-it-schrittmotor-nema14-01-neu-0-1-nm-0-4-a-wellen-durchmesser-5-mm-2142507.html)
- motor controllers - 1 time - 7.55 CHF - https://www.conrad.ch/de/p/iduino-st-1112-motortreiber-1-st-1525437.html (https://www.conrad.ch/de/p/iduino-st-1112-motortreiber-1-st-1525437.html)
- Solenoid - 1 time - 22 CHF - https://www.conrad.ch/de/p/intertec-its-ls2924b-d-12vdc-hubmagnet-drueckend-0-2-n-mm-10-22-n-mm-12-v-dc-4-5-w-502365.html (https://www.conrad.ch/de/p/intertec-its-ls2924b-d-12vdc-hubmagnet-drueckend-0-2-n-mm-10-22-n-mm-12-v-dc-4-5-w-502365.html)
- L298N (control the solenoid) - 1 time - 5 CHF - in stock
- Lead screw linear rail kit - 1 time - 40 CHF - in stock
- Rubber anti slip sheet - 1 time - 11.90 CHF - https://www.digitec.ch/en/s1/product/tamiya-rubber-anti-slip-sheet-rc-model-accessories-19587999 (https://www.digitec.ch/en/s1/product/tamiya-rubber-anti-slip-sheet-rc-model-accessories-19587999)
- Power supply - 1 time - 11.95 CHF - https://www.conrad.ch/de/p/voltcraft-sng-1000-oc-n-steckernetzteil-einstellbar-3-v-dc-4-5-v-dc-5-v-dc-6-v-dc-9-v-dc-12-v-dc-1-a-12-w-ausgangs-2266526.html (https://www.conrad.ch/de/p/voltcraft-sng-1000-oc-n-steckernetzteil-einstellbar-3-v-dc-4-5-v-dc-5-v-dc-6-v-dc-9-v-dc-12-v-dc-1-a-12-w-ausgangs-2266526.html)
- USB-C Power Supplies - 1 time - 10.40 CHF - https://www.digitec.ch/en/s1/product/intertech-pd-2020-20-w-quick-charge-30-usb-chargers-36200090 (https://www.digitec.ch/en/s1/product/intertech-pd-2020-20-w-quick-charge-30-usb-chargers-36200090)
- USB-C Cables - 1 time - 7.65 CHF - https://www.digitec.ch/en/s1/product/samsu ng-usb-c-usb-c-1-m-usb-20-usb-cables-11583637 (https://www.digitec.ch/en/s1/product/samsung-usb-c-usb-c-1-m-usb-20-usb-cables-11583637)
- Small magnets - 4 times - 8.25 CHF - https://www.digitec.ch/en/s1/product/tre ndform-kubiq-10-piece-magnets-6529972 (https://www.digitec.ch/en/s1/product/trendform-kubiq-10-piece-magnets-6529972)

Total cost: 209.40 CHF

## 4 Risk Assessment

In this section, we conduct a comprehensive risk assessment to identify potential challenges and vulnerabilities that could impede the success of our project. By evaluating technological risks we aim to proactively address these issues through strategic planning and prototype development. This assessment underscores our commitment to ensure the resilience and adaptability of our project, thereby minimizing the likelihood of failure and maximizing its overall effectiveness.

- Power supplies to steppers:
As mentioned in the manual, inadequate wiring practices and carelessness may lead to frying a computer or damaging the parts, especially the motor drivers and the stepper motors, potentially putting at risk the functionality of the project.
- Control of the solenoid:
While the solenoid allows for a completely vertical and uni-directional movement, since we don’t have experience with them, we’re not sure how precisely we can control the acceleration and force of the resulting movement. An alternative could be to use a stepper motor instead for pressing the remote buttons.
An additional risk could be that not all buttons require the same pressure. It could be difficult to adapt to this.
- Adaptability to different remotes:
The project’s adaptability to different remote controls is a challenge, as compatibility issues may arise with various types of remotes due to the vast spectrum of sizes. The amount of different size and shapes possible makes it complicated to design the clamp mechanism.
- Magnet interferences:
The presence of magnets in the project could disrupt the operation of sensitive electronic components such as the solenoid push-down mechanism, motors or the WiFi chip of the ESP32, leading to unpredictable behavior.
- WiFi network stability:
The reliance on WiFi connectivity on those ESP32 microcontrollers introduces a risk related to network instability, which could affect communication between project components.
- Ease of configuration:
The configuration and calibration of the plotter will have the possibility to be done in two ways: manually via the phone app or with computer vision via a computer. The manual setup may be time consuming for remotes with many buttons. The camera and computer vision setup may be hard to configure for non-technical users. This option also has its own additional challenges. The recognition of the remote and its buttons rely on the camera, the placement of the remote, the lightning of the room and overall restrictions due to remote design. These may affect the accuracy of the image recognition.
- Computer vision to button press precision:
Detecting the correct position and therefore being able to guarantee a precise button press while using computer vision to calibrate and configure the device could be difficult for the same reasons listed in above point.

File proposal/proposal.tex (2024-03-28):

\documentclass[12pt, a4paper, openany]{article}
\usepackage[utf8]{inputenc}
\usepackage[T1]{fontenc}

\usepackage{mfirstuc}

% LANGUAGE
\usepackage{enumitem}  % Enumerate improved

% MATH / Others
\usepackage{amsmath, amssymb}  % Math symbols
\usepackage{physics}  % \norm and \abs
\usepackage{esvect, cancel}  % Misc., vectors, strikethrough
\usepackage{mhchem}  % Chemistry
\usepackage{siunitx}  % Units SI
\usepackage{minted}  % Code fences ([cache=false])
\setminted[python]{
    fontsize=\footnotesize,
    tabsize=4,
    rulecolor=black,
    xleftmargin=18pt,
    linenos,
    breaklines
}
\usemintedstyle{pastie}

% GEOMETRY
\usepackage[
    paper=a4paper,
    top=2cm,
    left=2cm,
    headheight=15pt,
    headsep=12pt,
    textwidth=17cm,
    textheight=25.5cm,
]{geometry}
\usepackage{parskip}  % Reformat paragraphs, no indent first line
\usepackage{enumitem}  % Enumerate improved
\usepackage{scrextend}  % Indent text with addmargin environment
\usepackage{graphicx}  % Include graphics
\usepackage{wrapfig}
\graphicspath{{latex-img/}}
\usepackage{caption}  % Caption without figures
\usepackage{float}

\usepackage{paracol}

% HYPERLINKS
\PassOptionsToPackage{hyphens}{url}\usepackage{hyperref}
\hypersetup{
    colorlinks=true,
    linktoc=all,
    linkcolor=blue,
}
\usepackage{xurl}

\usepackage[bottom]{footmisc}

% HEADERS
\usepackage{fancyhdr}
    \pagestyle{fancy}
    \lhead{CS-358 MIT}
    \rhead{Helping Hand}
    \renewcommand{\footrulewidth}{0.4pt}
    \renewcommand{\headrulewidth}{0.4pt}
\usepackage{etoolbox}  % Define chapter page style
    \patchcmd{\chapter}{\thispagestyle{plain}}{\thispagestyle{fancy}}{}{}

% TITLE PAGE
\title{Helping Hand}
\author{Lucas Jung - IN BA6 324724\\Nour Guermazi - SC BA6 314474\\Pinar Oray - IN BA6 311543\\Jonas Sulzer - IN BA6 325554\\Yoan Giovannini - IN BA6 303934}
\date{2024 - 03}

\newcommand{\footlink}[2]{\href{#2}{#1}\footnote{{\MakeUppercase #1}: \url{#2}}}
\newcommand*{\fullref}[1]{\hyperref[{#1}]{\autoref*{#1} \nameref*{#1}}}

\begin{document}
\maketitle
\thispagestyle{fancy}
\pagenumbering{arabic}

\begin{center}
    \textbf{Beyond Accessibility: Unleashing the Potential of Home Automation to Foster Independence and Inclusivity for Individuals with Unique Needs}
\end{center}

\par\noindent\rule{\textwidth}{0.4pt}
\vspace{-20pt}
\tableofcontents
\par\noindent\rule{\textwidth}{0.4pt}

\vspace{10pt}

\input{idea.tex}
\newpage
\input{BOM.tex}
\newpage
\input{RAD.tex}

\end{document}

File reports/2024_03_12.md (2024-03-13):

# Meeting with TA

- Presentation, get to know each other
- Explain our project
- Be careful not to take too much space and make room for everyone in the team to express themselves

## Feedback

- We need to draw sketches
- Explain not only what, but also HOW.
- Present other use cases: Pinar's dad + regular home automation
- Think about the camera 2D plotter variant and decide
- Addition of IR re-player ?
- Project was accepted so it is good like that but think of making it even better and appealing
- Make it look beautiful

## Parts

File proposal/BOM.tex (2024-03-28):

\section{Bill of Materials}

The Bill of Materials (BOM) is a key part of our proposal, listing all required materials, quantities, specifications, and estimated costs.
It streamlines procurement, budgeting, and decision-making, showcasing our meticulous planning and resource management.

\begin{itemize}
    \item ESP32 C6 - 1 time - 12.95 CHF - \url{https://www.conrad.ch/de/p/espressif-esp32-c6-devkitc-1-n8-entwicklungsboard-espressif-2992162.html}
    \item ESP32 CAM - 1 time - 13 CHF - in stock
    \item NEMA 14 motors - 2 times - 17 CHF - \url{https://www.conrad.ch/de/p/joy-it-schrittmotor-nema14-01-neu-0-1-nm-0-4-a-wellen-durchmesser-5-mm-2142507.html}
    \item motor controllers - 1 time - 7.55 CHF - \url{https://www.conrad.ch/de/p/iduino-st-1112-motortreiber-1-st-1525437.html}
    \item Solenoid - 1 time - 22 CHF - \url{https://www.conrad.ch/de/p/intertec-its-ls2924b-d-12vdc-hubmagnet-drueckend-0-2-n-mm-10-22-n-mm-12-v-dc-4-5-w-502365.html}
    \item L298N (control the solenoid) - 1 time - 5 CHF - in stock
    \item Lead screw linear rail kit - 1 time - 40 CHF - in stock
    \item Rubber anti slip sheet - 1 time - 11.90 CHF - \url{https://www.digitec.ch/en/s1/product/tamiya-rubber-anti-slip-sheet-rc-model-accessories-19587999}
    \item Power supply - 1 time - 11.95 CHF - \url{https://www.conrad.ch/de/p/voltcraft-sng-1000-oc-n-steckernetzteil-einstellbar-3-v-dc-4-5-v-dc-5-v-dc-6-v-dc-9-v-dc-12-v-dc-1-a-12-w-ausgangs-2266526.html}
    \item USB-C Power Supplies - 1 time - 10.40 CHF - \url{https://www.digitec.ch/en/s1/product/intertech-pd-2020-20-w-quick-charge-30-usb-chargers-36200090}
    \item USB-C Cables - 1 time - 7.65 CHF - \url{https://www.digitec.ch/en/s1/product/samsung-usb-c-usb-c-1-m-usb-20-usb-cables-11583637}
    \item Small magnets - 4 times - 8.25 CHF - \url{https://www.digitec.ch/en/s1/product/trendform-kubiq-10-piece-magnets-6529972}
\end{itemize}

Total cost: \textbf{209.40 CHF}

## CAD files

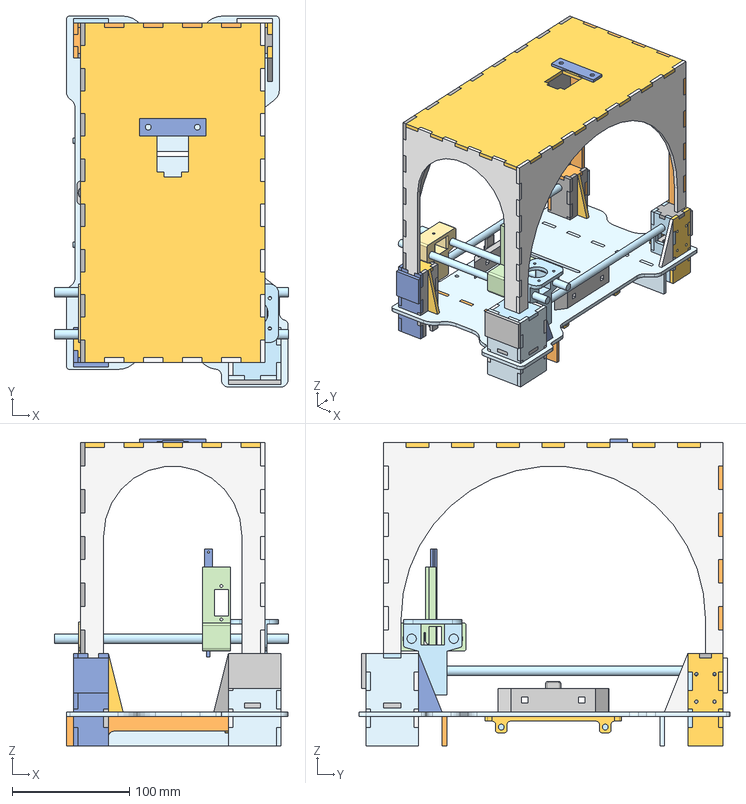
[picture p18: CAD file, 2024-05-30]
design/assembly.step
200.0 x 317.0 x 262.0 mm
c3 top
left c2-c4
back c3-c4
metal rod x 4
column 2 belt holder bottom
c1 left
c1 right
axis_holder_east
c1 front
right c1-c3
screw top mockup
c3 right support (front view)
c4 cover
clamp rod mockup x 2
Base holder
c4 top
c3 cover
c2 back
c4 right
base (top view)
c3 back
c2 left
c4 back
3D cam holder
c3 left
bar holder short left on assembly
axis_holder_west
moving clamp side
c3 right
c3 front
c2 cover
c4 back support (right view)
c3 to c4 base support (front view)
c1 right support (front view)
c1 top
c2 front support(right view)
bar holder short right on assembly
column 2 belt holder top
stick
belt_cart
c4 left support (front view)
c1 to c2 base support (front view)
bar holder long
c1 back
c2 right
c2 left support (front view)
c2 top
screw attachment
c4 front
fixed side attachement
c1 cover
c2 front
front c1-c2
c4 left
top face
motor mount (top view)

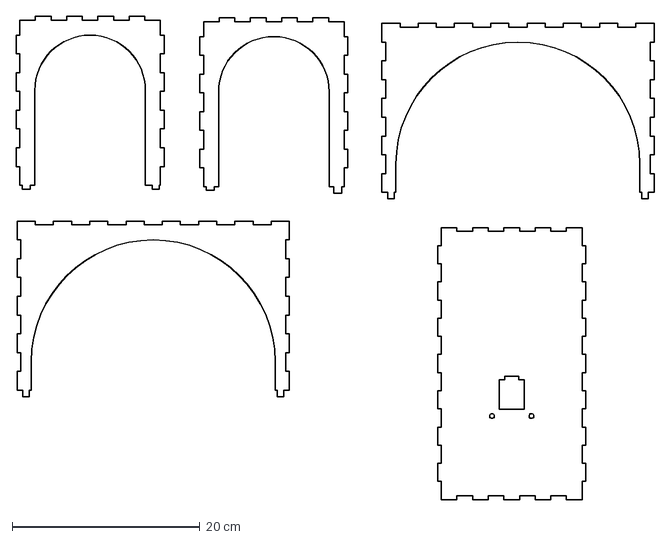
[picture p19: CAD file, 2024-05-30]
design/camholder.dxf
68.0 x 51.5 cm

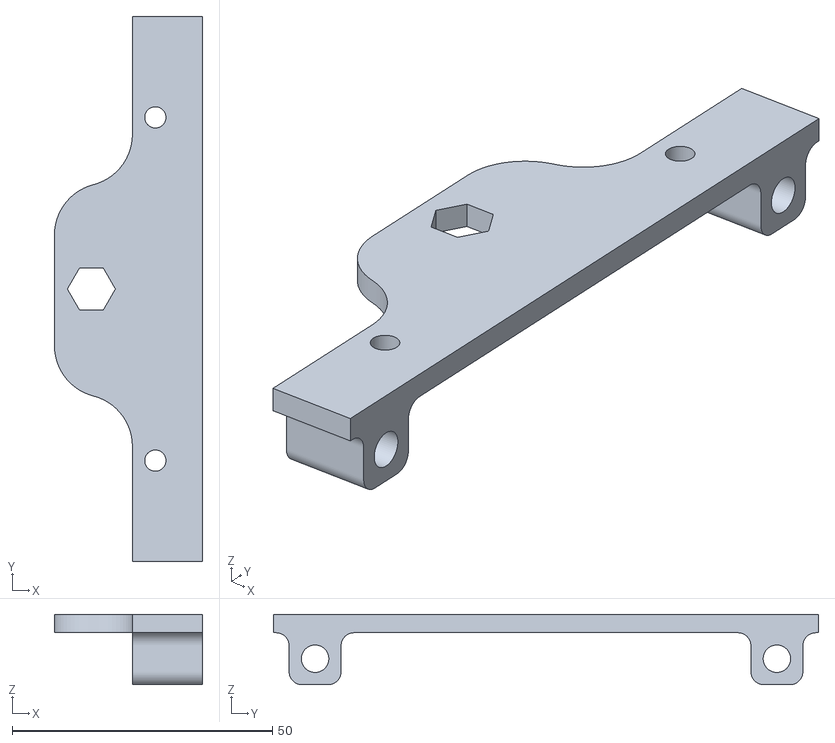
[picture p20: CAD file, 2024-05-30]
design/clamp/moving_side_bottom.stl
28.5 x 104.8 x 13.6

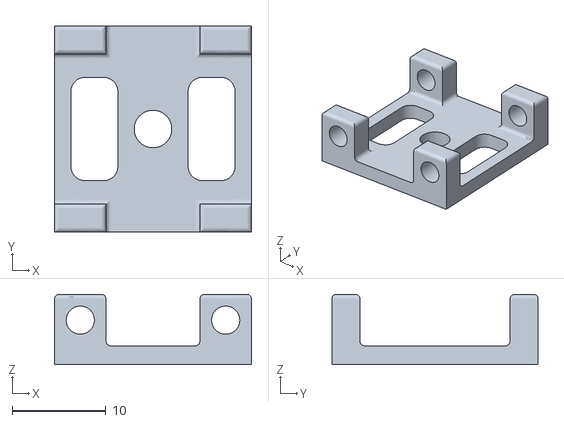
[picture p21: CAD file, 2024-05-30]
design/plotter/plotter_column_2_belt_holder_top.stl
21.0 x 22.0 x 7.50

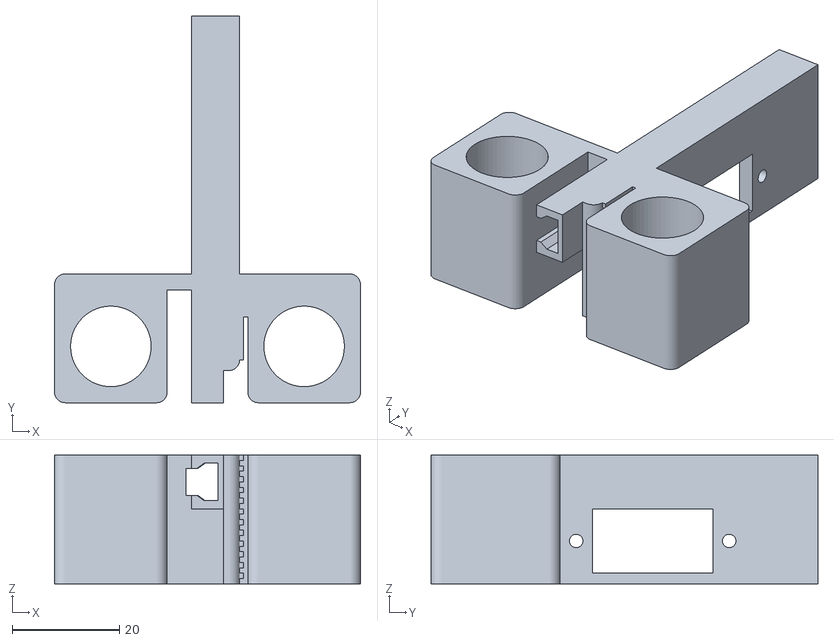
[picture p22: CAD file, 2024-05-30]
design/y_axis/belt_cart.stl
57.0 x 72.0 x 24.0

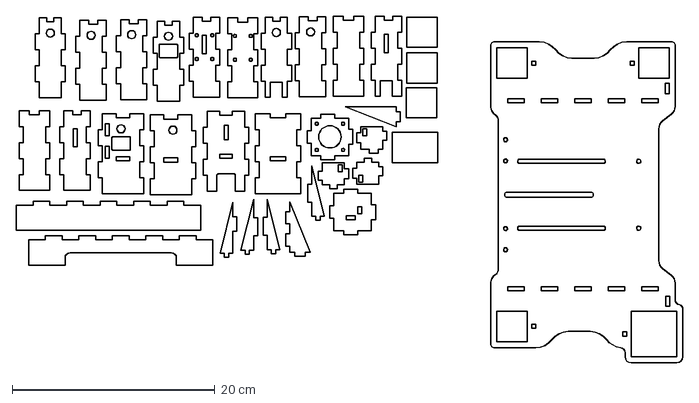
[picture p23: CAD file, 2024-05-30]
design/plotter/plotter.dxf
65.8 x 34.2 cm

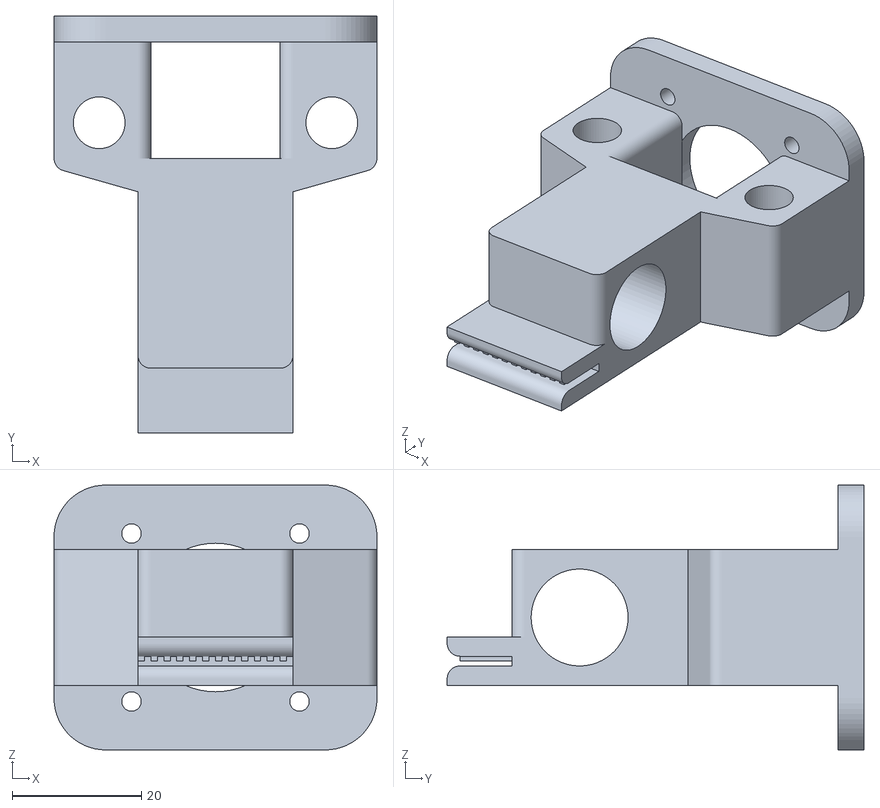
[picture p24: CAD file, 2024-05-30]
design/y_axis/axis_holder_west.stl
50.0 x 64.5 x 41.0

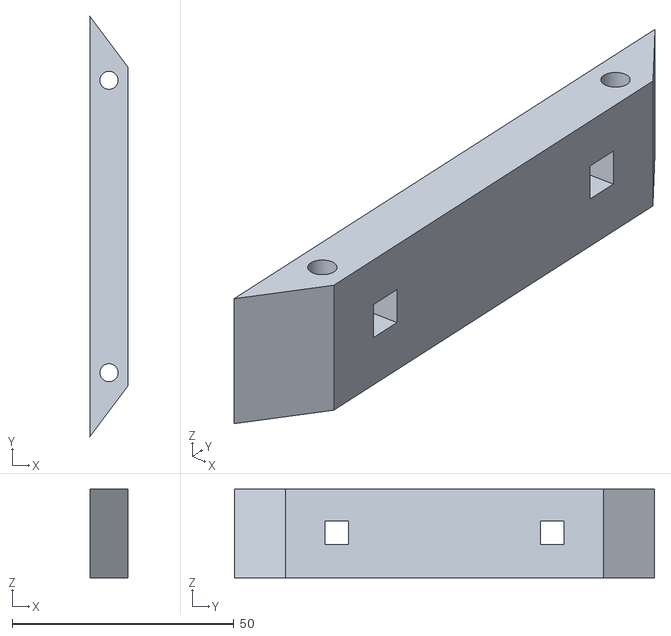
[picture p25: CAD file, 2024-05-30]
design/clamp/clamp_fixed_side.stl
8.60 x 94.8 x 20.0

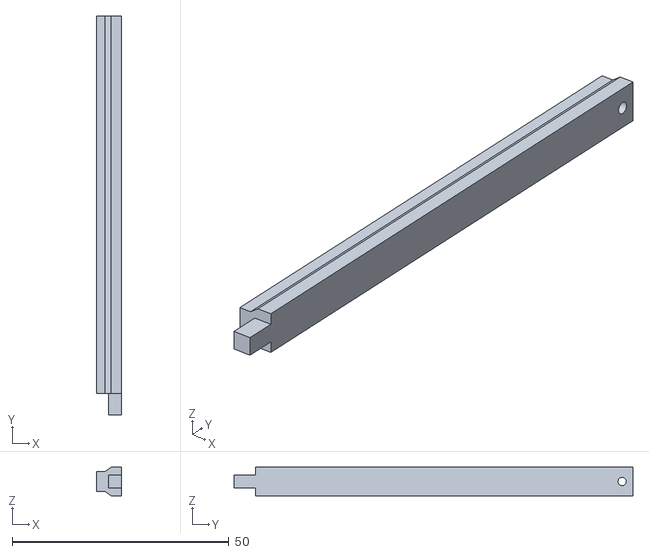
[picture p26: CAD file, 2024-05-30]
design/y_axis/stick.stl
5.80 x 92.0 x 6.60

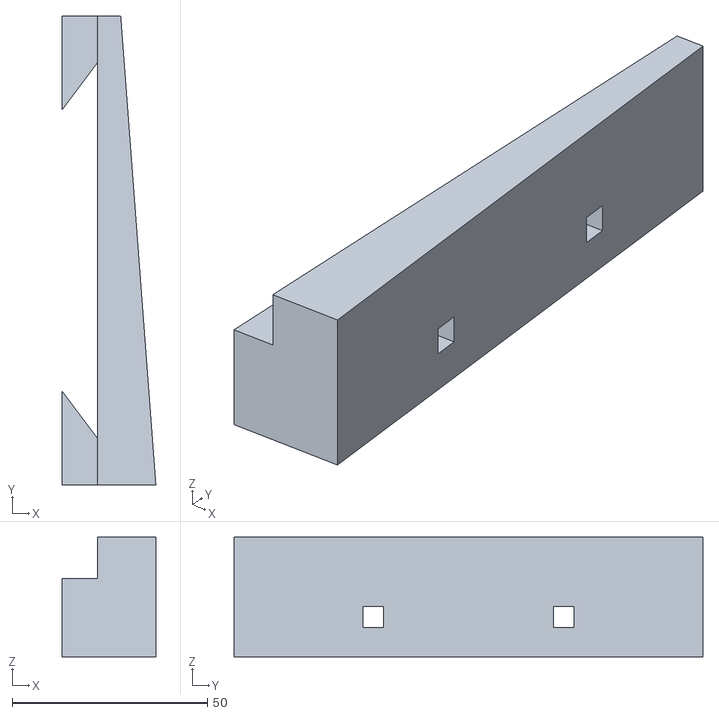
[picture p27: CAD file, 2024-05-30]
design/clamp/clamp_inclined_left.stl
24.0 x 120.0 x 30.6

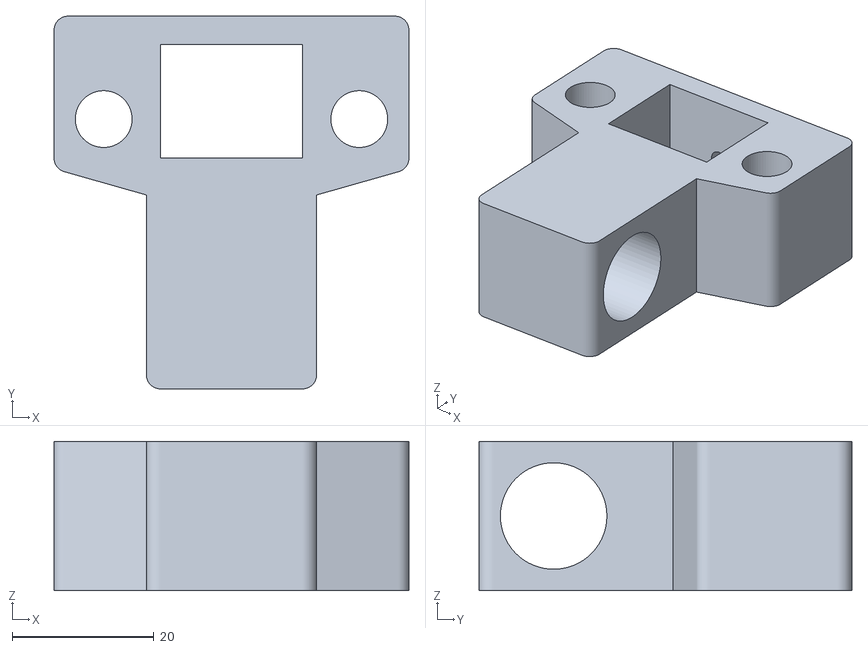
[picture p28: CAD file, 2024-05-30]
design/y_axis/axis_holder_east.stl
50.0 x 52.5 x 21.0

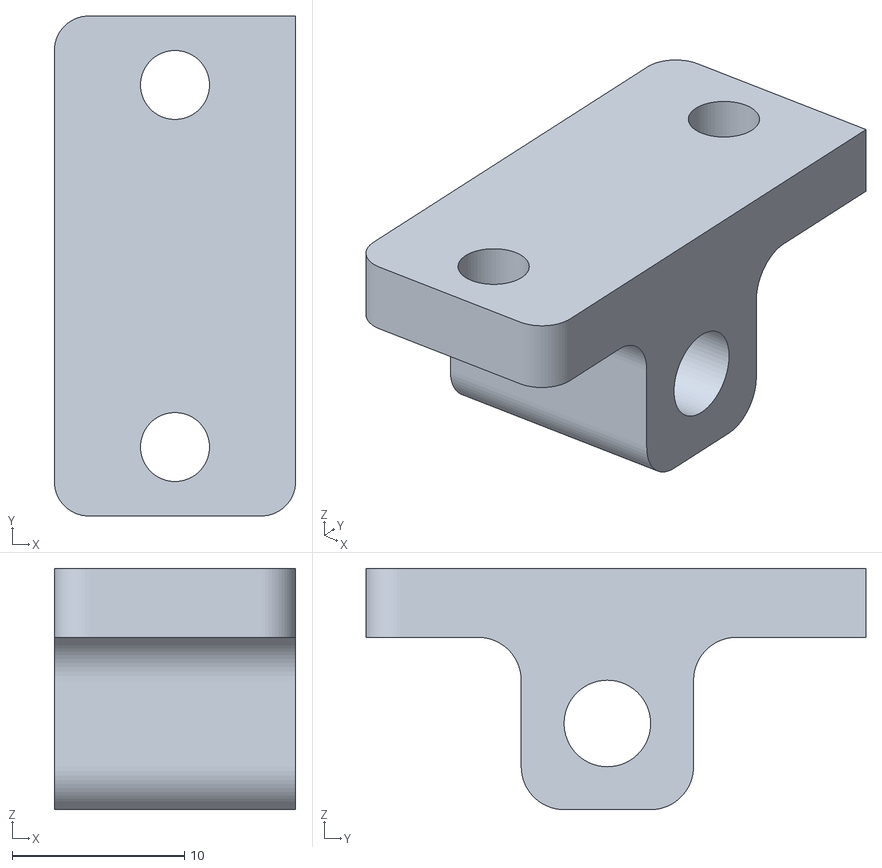
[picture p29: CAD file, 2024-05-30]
design/clamp/bar_holder_short_left.stl
14.0 x 29.0 x 14.0

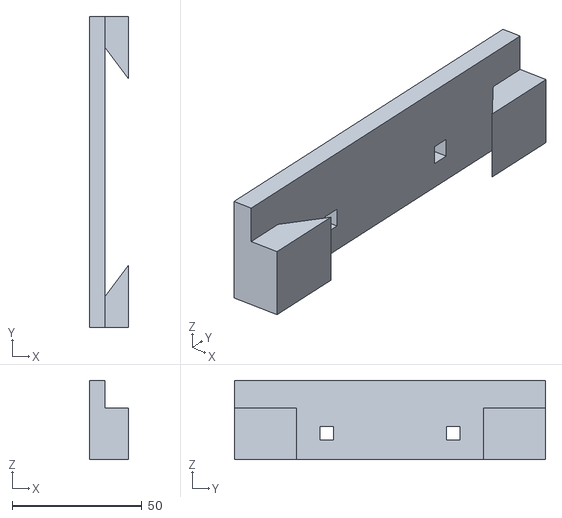
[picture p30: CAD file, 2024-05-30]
design/clamp/clamp_parallel_right.stl
15.0 x 120.0 x 30.6

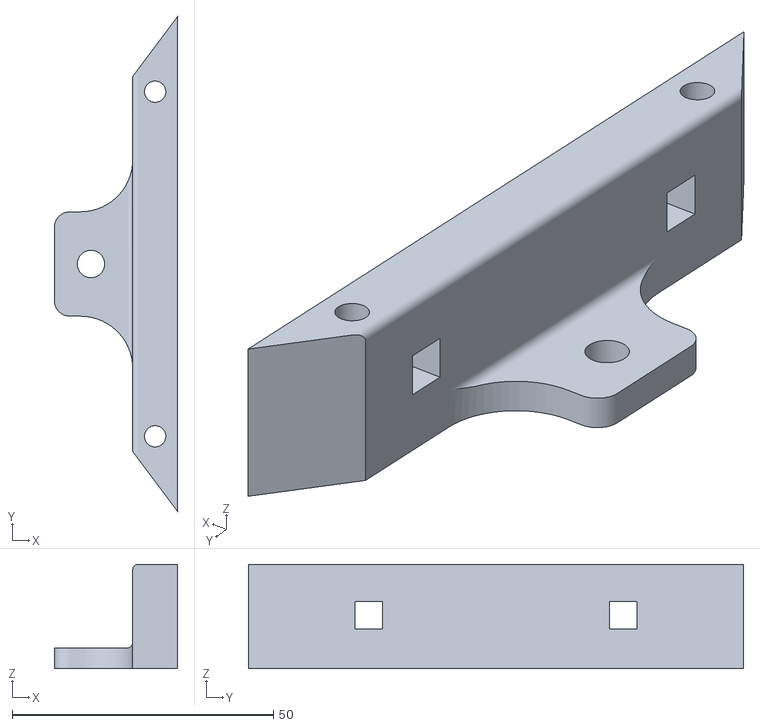
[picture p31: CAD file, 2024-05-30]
design/clamp/clamp_moving_top.stl
23.6 x 94.8 x 20.0

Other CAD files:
design/plotter/plotter_column_2_gear_holder_bottom.stl
design/clamp/clamp_elliptic_right.stl
design/clamp/fixed_side_bottom.stl
design/clamp/clamp_elliptic_left.stl
design/assembly.x_t
design/clamp/bar_holder_short_right.stl
design/clamp/clamp_inclined_right.stl
design/clamp/clamp_parallel_left.stl
design/clamp/screw_top_attachment.stl

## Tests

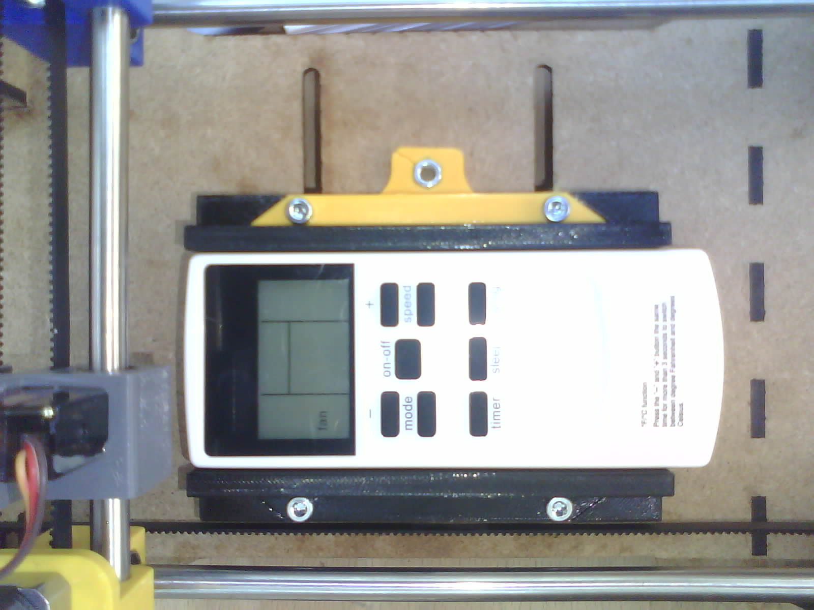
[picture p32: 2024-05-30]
code/CVserver/images_test/remote_1.jpg

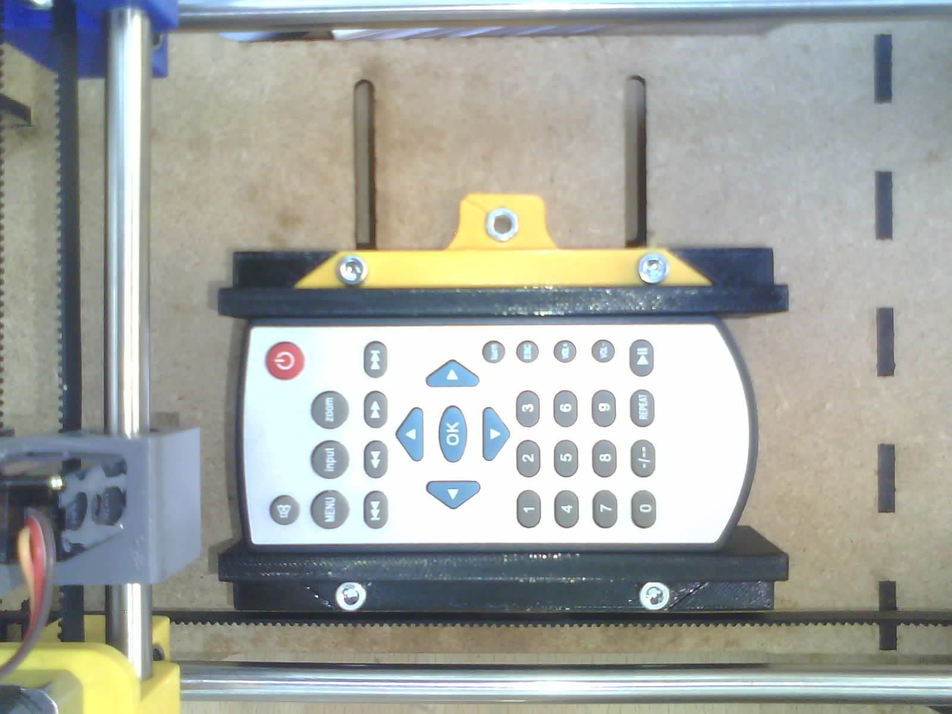
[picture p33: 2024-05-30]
code/CVserver/images_test/remote_2.jpg

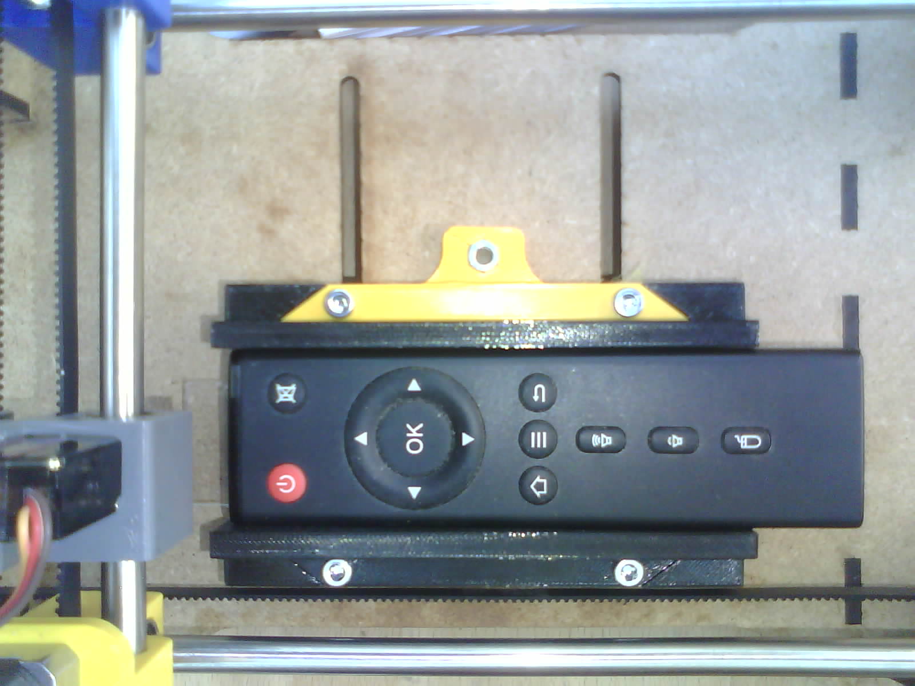
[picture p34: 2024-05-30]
code/CVserver/images_test/remote_5.jpg

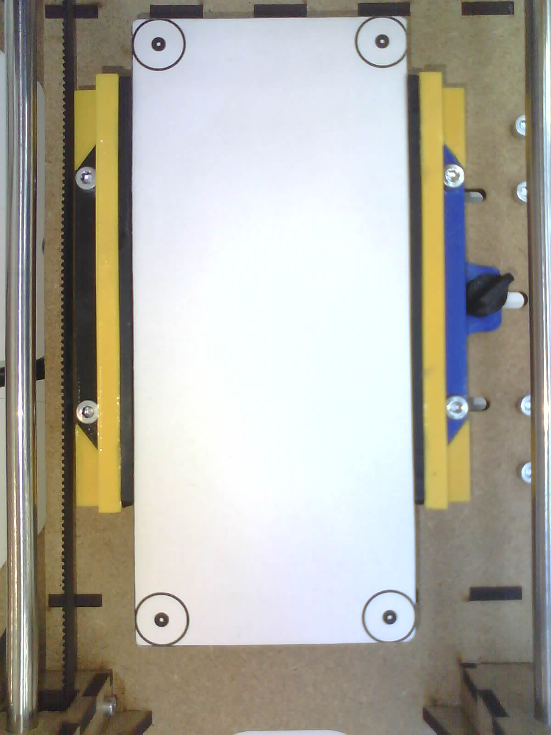
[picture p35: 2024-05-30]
code/CVserver/coords_test/calibration_capture.jpg

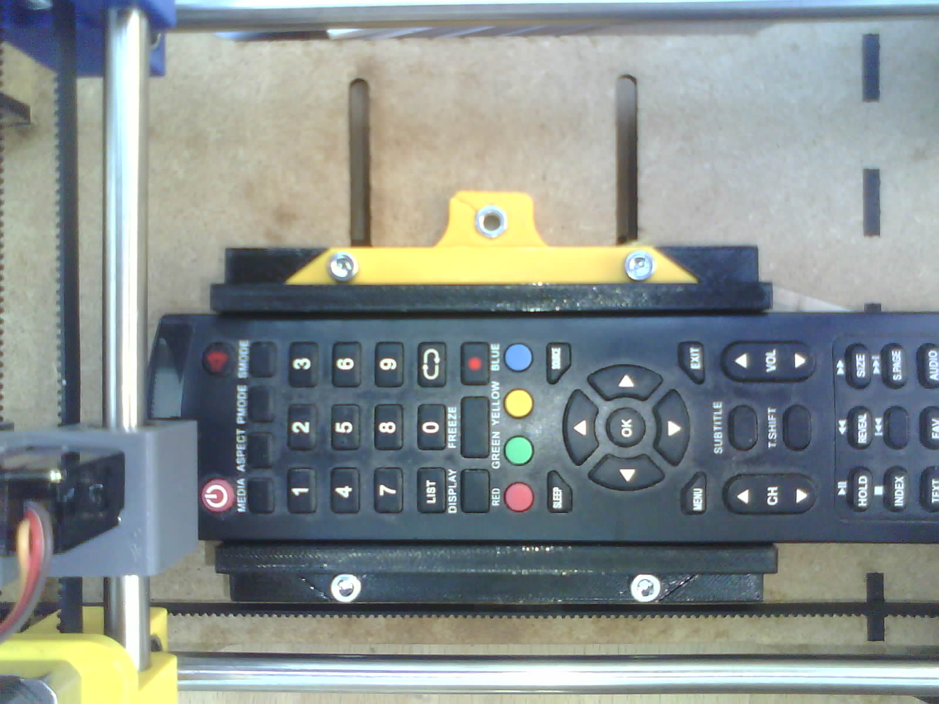
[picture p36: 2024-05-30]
code/CVserver/images_test/remote_4.jpg

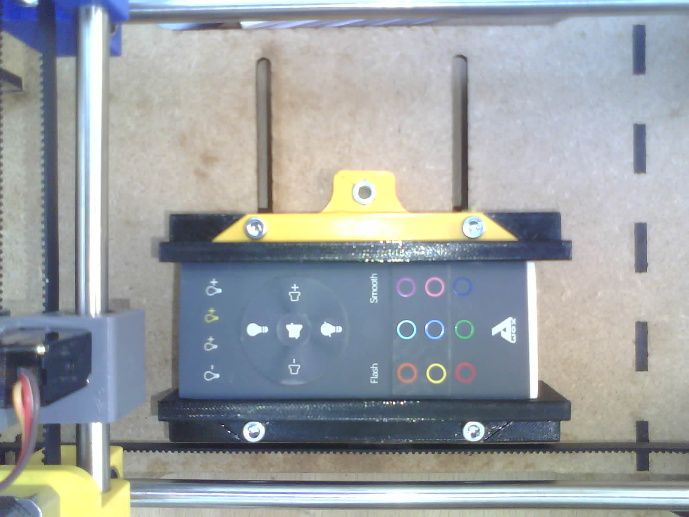
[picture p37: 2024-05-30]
code/CVserver/images_test/remote_3.jpg

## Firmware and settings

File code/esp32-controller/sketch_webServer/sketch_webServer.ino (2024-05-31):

/**
Simple web server

credits:
WiFiWebServer usage: https://github.com/khoih-prog/WiFiWebServer/tree/master
Preferences usage: https://github.com/vshymanskyy/Preferences
*/
//#include <ESPmDNS.h>
#include <Preferences.h>
#include <WiFi.h>
#include <WebServer.h>
#include <AccelStepper.h>
#include <MultiStepper.h>
//#include <Servo.h>
#define MotorInterfaceType 1

//blue led port
#define LED_BLUE 16

//max size of the string containing the coordinates
#define COORDSTRINGSIZE 15

//server hostname (without the .local)
const char* hostname = "plottercontroller";

//storage of wifi credentials
const char* appNamespace = "web-server";
Preferences preferences;

//motors parameters: DO NOT USE 25 & 26 pins
AccelStepper X(MotorInterfaceType, 0, 4); //0: step, 4: direction
AccelStepper Y(MotorInterfaceType, 20, 21); //20: step, 21: direction
MultiStepper XY;
#define MOTOR_MAX_SPEED 200.0
#define CALIBRATION_MAX_SPEED 25.0
const int MAX_X = 400;
const int MAX_Y = 1000;
const int MOVE_OUT_X = 0;
const int MOVE_OUT_Y = 0;

//servo parameters
const int SERVO_PIN = 18;
const int UP_TIME = 2000;
const int PRESS_TIME = 1800;
const int SERVO_SHORT_DELAY = 300; //in ms
const int SERVO_LONG_DELAY = 1500; //in ms
const int SERVO_DELAY = 300; //in ms (delay for the servo to move)
const int SERVO_BALANCE = 20000;
//Servo servo;

//pin for the plotter limit
const int LIMIT_PIN = 23;
const int POS_STEP = 5;
const int CALBRATION_DELAY = 200; //delay between x and y calibration in ms

//plotter position
int position[2] = {0, 0};

/*
Setup the servo
*/
void servoSetup() {
  pinMode(SERVO_PIN, OUTPUT);
  moveServo(UP_TIME);
}

void moveServo(int time){
  delay(SERVO_DELAY);
  digitalWrite(SERVO_PIN, HIGH);
  delayMicroseconds(time);
  digitalWrite(SERVO_PIN, LOW);
  delayMicroseconds(SERVO_BALANCE - time);
  delay(SERVO_DELAY);
}

/*
Setup the motors
*/
void motorsSetup(float max_speed) {
  XY = MultiStepper();
  X.setMaxSpeed(max_speed);
  Y.setMaxSpeed(max_speed);
  XY.addStepper(X);
  XY.addStepper(Y);
}

/*
Setup the wifi connection
*/
void wifiSetup() {
  preferences.begin(appNamespace, true);
  String ssid = preferences.getString("ssid", "");
  String password = preferences.getString("password", "");
  preferences.end();
  Serial.print("ssid: ");
  Serial.println(ssid.c_str());
  Serial.print("password: ");
  Serial.println(password.c_str());
  WiFi.begin(ssid.c_str(), password.c_str());
  Serial.print("Connecting");
  while (WiFi.status() != WL_CONNECTED)
  {
    digitalWrite(LED_BLUE,HIGH);
    delay(500);
    digitalWrite(LED_BLUE,LOW);
    delay(500);
    Serial.print(".");
  }
  /*if (!MDNS.begin(hostname)) {   // Set the hostname to hostname + ".local"
    Serial.println("Error setting up the hostname (MDNS)!");
  } else {
    Serial.println();
  }*/
  Serial.print("Connected\nIP address: ");
  Serial.println(WiFi.localIP());
  Serial.print("Hostname: ");
  Serial.print(hostname);
  Serial.println(".local");
}


WebServer server(80);
const char* rootPath = "/";
const char* moveToPath = "/go-to";
const char* shortPressPath = "/short-press";
const char* longPressPath = "/long-press";
const char* moveOutPath = "/move-out";
const char* discoveryPath = "/discovery-hh";

/**
Setup the web server
*/
void webServerSetup() {
  server.enableCORS();
  server.on(F(rootPath), handleRoot);
  server.on(F(moveToPath), handleMoveTo);
  server.on(F(shortPressPath), handleShortPress);
  server.on(F(longPressPath), handleLongPress);
  server.on(F(moveOutPath), handleMoveOut);
  server.on(F(discoveryPath), handleDiscovery);
  server.onNotFound(handleNotFound);
  server.begin();
  Serial.println("Web server started");
}

/**
Calibrate the plotter origin
*/
void calibrate(){
  pinMode(LIMIT_PIN, INPUT_PULLUP);

  //x
  while(!digitalRead(LIMIT_PIN)){
    position[0] -= POS_STEP;
    goTo(position[0], position[1]);
  }
  Serial.println("X");
  while(digitalRead(LIMIT_PIN)){
    position[0] += POS_STEP;
    goTo(position[0], position[1]);
  }
  Serial.println("NX");
  delay(CALBRATION_DELAY);
  //y
  while(!digitalRead(LIMIT_PIN)){
    position[1] -= POS_STEP;
    goTo(position[0], position[1]);
  }
  Serial.println("Y");
  while(digitalRead(LIMIT_PIN)){
    position[1] += POS_STEP;
    goTo(position[0], position[1]);
  }
  Serial.println("NY");
  position[0] = 0;
  position[1] = 0;
  X.setCurrentPosition(0);
  Y.setCurrentPosition(0);
}

void setup() {
  Serial.begin(115200);
  Serial.println();
  delay(1000); //delay so that the first string is printed
  Serial.println("HELLO");
  pinMode(LED_BLUE, OUTPUT);
  servoSetup();
  motorsSetup(CALIBRATION_MAX_SPEED);
  calibrate();
  motorsSetup(MOTOR_MAX_SPEED);
  //testMotorsSpeed();
  wifiSetup();
  webServerSetup();
}

void testMotorsSpeed(){
  for(int i = 0; i < 10; i++){
    goTo(0, 1000);
    calibrate();
    XY = MultiStepper();
    motorsSetup(i * 10 + 400);
  }
  
}

/*
Move the motors the the (x,y) position
*/
void goTo(int x, int y) {
  long pos[2] = {x,y};
  XY.moveTo(pos);
  XY.runSpeedToPosition();
  while(X.distanceToGo() != 0 || Y.distanceToGo() != 0){} //wait for the plotter to stop
}

/**
convert coordinates to string
*/
void coordinatesToString(int* coordinates, char result[COORDSTRINGSIZE]){
  sprintf(result, "%d, %d", coordinates[0], coordinates[1]);
}

/**
Handle the web page at /
*/
void handleRoot() {
  digitalWrite(LED_BLUE, HIGH);
  if(isGet()){
    char str[COORDSTRINGSIZE];
    coordinatesToString(position, str);
    String message = String("hello world\n");
    message += str;
    server.send(200, F("text/plain"), message.c_str());
  }
  digitalWrite(LED_BLUE, LOW);
}

/**
Handle the web page at /move-to
*/
void handleMoveTo() {
  digitalWrite(LED_BLUE, HIGH);
  if(isGet()){
    int coord[2] = {0,0};
    coord[0] = atoi(server.arg("x").c_str());
    coord[1] = atoi(server.arg("y").c_str());
    if(coord[0] < 0) coord[0] = 0;
    if(coord[1] < 0) coord[1] = 0;
    if(coord[0] > MAX_X) coord[0] = MAX_X;
    if(coord[1] > MAX_Y) coord[1] = MAX_Y;
    position[0] = coord[0];
    position[1] = coord[1];
    goTo(coord[0], coord[1]);
    Serial.println(coord[0]);
    Serial.println(coord[1]);
    server.send(200, F("text/plain"), "OK");
  }
  digitalWrite(LED_BLUE, LOW);
}

/**
Handle the web page at /discovery-hh
Returns device type (PLO) and the mac address
*/
void handleDiscovery() {
  if(isGet()){
    String message = String("PLO");
    message += ",";
    message += WiFi.macAddress();
    server.send(200, F("text/plain"), message.c_str());
  }
}

//move out of the remote
void handleMoveOut() {
  goTo(MOVE_OUT_X, MOVE_OUT_Y);
  int coord[2] = {MOVE_OUT_X, MOVE_OUT_Y};
  position[0] = 0;
  position[1] = 0;
  server.send(200, F("text/plain"), "OK");
}

//execute short press
void handleShortPress() {
  moveServo(PRESS_TIME);
  delay(SERVO_SHORT_DELAY);
  moveServo(UP_TIME);
  server.send(200, F("text/plain"), "OK");
}

//execute long press
void handleLongPress() {
  moveServo(PRESS_TIME);
  delay(SERVO_LONG_DELAY);
  moveServo(UP_TIME);
  server.send(200, F("text/plain"), "OK");
}

void handleNotFound() {
  server.send(404, F("text/plain"), "404 not found");
}

/**
Check if it's a get request. Send back an error if not.
*/
bool isGet(){
  if(server.method() != HTTP_GET){
    server.send(405, F("text/plain"), F("Method not allowed"));
    return false;
  }
  return true;
}


void loop() {
  server.handleClient();
}

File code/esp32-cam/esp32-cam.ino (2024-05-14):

#include "esp_camera.h"
#include <WiFi.h>

//
// WARNING!!! PSRAM IC required for UXGA resolution and high JPEG quality
//            Ensure ESP32 Wrover Module or other board with PSRAM is selected
//            Partial images will be transmitted if image exceeds buffer size
//
//            You must select partition scheme from the board menu that has at least 3MB APP space.
//            Face Recognition is DISABLED for ESP32 and ESP32-S2, because it takes up from 15 
//            seconds to process single frame. Face Detection is ENABLED if PSRAM is enabled as well

// ===================
// Select camera model
// ===================
//#define CAMERA_MODEL_WROVER_KIT // Has PSRAM
//#define CAMERA_MODEL_ESP_EYE // Has PSRAM
//#define CAMERA_MODEL_ESP32S3_EYE // Has PSRAM
//#define CAMERA_MODEL_M5STACK_PSRAM // Has PSRAM
//#define CAMERA_MODEL_M5STACK_V2_PSRAM // M5Camera version B Has PSRAM
//#define CAMERA_MODEL_M5STACK_WIDE // Has PSRAM
//#define CAMERA_MODEL_M5STACK_ESP32CAM // No PSRAM
//#define CAMERA_MODEL_M5STACK_UNITCAM // No PSRAM
#define CAMERA_MODEL_AI_THINKER // Has PSRAM
//#define CAMERA_MODEL_TTGO_T_JOURNAL // No PSRAM
//#define CAMERA_MODEL_XIAO_ESP32S3 // Has PSRAM
// ** Espressif Internal Boards **
//#define CAMERA_MODEL_ESP32_CAM_BOARD
//#define CAMERA_MODEL_ESP32S2_CAM_BOARD
//#define CAMERA_MODEL_ESP32S3_CAM_LCD
//#define CAMERA_MODEL_DFRobot_FireBeetle2_ESP32S3 // Has PSRAM
//#define CAMERA_MODEL_DFRobot_Romeo_ESP32S3 // Has PSRAM
#include "camera_pins.h"

// ===========================
// Enter your WiFi credentials
// ===========================
const char* ssid = "SPOT-iot";
const char* password = "";

void startCameraServer();
void setupLedFlash(int pin);

void setup() {
  Serial.begin(115200);
  Serial.setDebugOutput(true);
  Serial.println();

  camera_config_t config;
  config.ledc_channel = LEDC_CHANNEL_0;
  config.ledc_timer = LEDC_TIMER_0;
  config.pin_d0 = Y2_GPIO_NUM;
  config.pin_d1 = Y3_GPIO_NUM;
  config.pin_d2 = Y4_GPIO_NUM;
  config.pin_d3 = Y5_GPIO_NUM;
  config.pin_d4 = Y6_GPIO_NUM;
  config.pin_d5 = Y7_GPIO_NUM;
  config.pin_d6 = Y8_GPIO_NUM;
  config.pin_d7 = Y9_GPIO_NUM;
  config.pin_xclk = XCLK_GPIO_NUM;
  config.pin_pclk = PCLK_GPIO_NUM;
  config.pin_vsync = VSYNC_GPIO_NUM;
  config.pin_href = HREF_GPIO_NUM;
  config.pin_sccb_sda = SIOD_GPIO_NUM;
  config.pin_sccb_scl = SIOC_GPIO_NUM;
  config.pin_pwdn = PWDN_GPIO_NUM;
  config.pin_reset = RESET_GPIO_NUM;
  config.xclk_freq_hz = 20000000;
  config.frame_size = FRAMESIZE_UXGA;
  config.pixel_format = PIXFORMAT_JPEG; // for streaming
  //config.pixel_format = PIXFORMAT_RGB565; // for face detection/recognition
  config.grab_mode = CAMERA_GRAB_WHEN_EMPTY;
  config.fb_location = CAMERA_FB_IN_PSRAM;
  config.jpeg_quality = 12;
  config.fb_count = 1;
  
  // if PSRAM IC present, init with UXGA resolution and higher JPEG quality
  //                      for larger pre-allocated frame buffer.
  if(config.pixel_format == PIXFORMAT_JPEG){
    if(psramFound()){
      config.jpeg_quality = 10;
      config.fb_count = 2;
      config.grab_mode = CAMERA_GRAB_LATEST;
    } else {
      // Limit the frame size when PSRAM is not available
      config.frame_size = FRAMESIZE_SVGA;
      config.fb_location = CAMERA_FB_IN_DRAM;
    }
  } else {
    // Best option for face detection/recognition
    config.frame_size = FRAMESIZE_240X240;
#if CONFIG_IDF_TARGET_ESP32S3
    config.fb_count = 2;
#endif
  }

#if defined(CAMERA_MODEL_ESP_EYE)
  pinMode(13, INPUT_PULLUP);
  pinMode(14, INPUT_PULLUP);
#endif

  // camera init
  esp_err_t err = esp_camera_init(&config);
  if (err != ESP_OK) {
    Serial.printf("Camera init failed with error 0x%x", err);
    return;
  }

  sensor_t * s = esp_camera_sensor_get();
  // initial sensors are flipped vertically and colors are a bit saturated
  if (s->id.PID == OV3660_PID) {
    s->set_vflip(s, 1); // flip it back
    s->set_brightness(s, 1); // up the brightness just a bit
    s->set_saturation(s, -2); // lower the saturation
  }
  // set initial capture resolution
  if(config.pixel_format == PIXFORMAT_JPEG){
    s->set_framesize(s, FRAMESIZE_UXGA);
  }

#if defined(CAMERA_MODEL_M5STACK_WIDE) || defined(CAMERA_MODEL_M5STACK_ESP32CAM)
  s->set_vflip(s, 1);
  s->set_hmirror(s, 1);
#endif

#if defined(CAMERA_MODEL_ESP32S3_EYE)
  s->set_vflip(s, 1);
#endif

// Setup LED FLash if LED pin is defined in camera_pins.h
#if defined(LED_GPIO_NUM)
  setupLedFlash(LED_GPIO_NUM);
#endif

  WiFi.setHostname("helping-hand-cam");
  WiFi.begin(ssid, password);
  WiFi.setSleep(false);

  while (WiFi.status() != WL_CONNECTED) {
    delay(500);
    Serial.print(".");
  }
  Serial.println("");
  Serial.println("WiFi connected");

  startCameraServer();

  Serial.print("Camera Ready! Use 'http://");
  Serial.print(WiFi.localIP());
  Serial.println("' to connect");
  
}

void loop() {
  // Do nothing. Everything is done in another task by the web server
  delay(100000);
}

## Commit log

2024-03-19 feat(proposal): BOM + RAD + discuss for meeting
2024-03-23 feat(proposal): improved BOM + idea
2024-03-28 👌 IMPROVE: reworked project proposal idea
    - optionally attach a camera to assist the setup with computer vision on a computer
    - more flexible, plotter-like design
2024-03-28 👌 IMPROVE: explain that the plotter uses a selenoid actuator to precisely press the remote buttons
2024-03-28 👌 IMPROVE: better explain manual configuration process
2024-03-28 👌 IMPROVE: small changes according to review
2024-03-28 🐛 FIX: add missing dash ('-')
2024-03-28 🐛 FIX: typo
2024-03-28 🐛 FIX: some more typos
2024-03-28 update bill of material, missing: power supply
2024-03-28 add power supply
2024-03-28 👌 IMPROVE: include drawings of the concept into the proposal
2024-03-28 👌 IMPROVE: updated build of proposal.pdf
2024-03-31 👌 IMPROVE: clarify multiple/single box
    clarify that while we'll only build one device during the course,
    the idea and design is still for a user to be able to installl
    multiple boxes and have them work together from a single app
    those points have to be taken into account during the whole process
2024-03-31 📦 NEW: add a point to RAD concerning the selenoid
2024-03-31 📦 NEW: add a point to RAD concerning computer vision to button press precision
2024-03-31 📦 NEW: improved design sketches
2024-03-31 👌 IMPROVE: add phrase to RAD concerning pressure required to press buttons
2024-03-31 👌 IMPROVE: updated compiled project proposal pdf
2024-04-26 add stepper support: go-to and move-out endpoints
2024-04-26 add servo support
2024-04-30 feat(discovery): adds state for discovered devices
2024-05-02 add calibration function
2024-05-03 add electric schema
    [electric_schema.fzz]
2024-05-07 adjust constants & fix position bug
    [sketch_webServer.ino]
2024-05-14 first version of camera setup
2024-05-14 📦 NEW: setup arduino project with all (provided sample) files for it to compile
    [partitions.csv]
2024-05-14 📦 NEW: add Readme with setup instructions
2024-05-14 👌 IMPROVE: remove manual attempt at activating the flash
    this can already be done currently over the following (default) endpoint:
    /control?var=led_intensity&val=255
2024-05-14 👌 IMPROVE: remove unused face detection/recognitio code
2024-05-14 👌 IMPROVE: disable all unneeded endpoints except if debug mode is enabled
2024-05-14 📦 NEW: add led-flash intensity endpoint
    this alows to disable and enable the led
    allowed intensity values are from 0 to 255
    `/led-flash?intensity=255`
2024-05-14 👌 IMPROVE: set default flash value to halph intensity
2024-05-14 👌 IMPROVE: set resolution to highest available one on ESP32-CAM
2024-05-14 🐛 FIX: remove unused include
    [esp32-cam.ino]
2024-05-14 📦 NEW: add wiring schema for esp32cam
    [esp32-cam-flashing.fzz]
2024-05-17 feat(calibration): setup calibration for the app
2024-05-17 📦 NEW: SAM segmantic analysis using facebooks model
2024-05-22 feat(calibration): try to move motors using the app
2024-05-24 feat(calibration): tried calibration again
2024-05-27 feat(calibration): improve cv server test files
2024-05-28 feat(calibration): new remote area parameters
2024-05-28 add all design files
    [axis_holder_east.stl, axis_holder_west.stl, bar_holder_short_left.stl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]
2024-05-28 docs: images of assembly
2024-05-28 docs: update plotter drawing with rod cover
    [plotter.dxf]
2024-05-28 docs: images of wiring + assembly to README
2024-05-28 docs: assembly step file
    [assembly.step]
2024-05-30 feat(calibration): finish calibration
2024-05-30 📦 NEW: filter output of sam and tansform to expected output
2024-05-30 👌 IMPROVE: rotation, better filtering, specify sampling area
2024-05-30 👌 IMPROVE: latest calibration as of 2024.05.30 16:30
2024-05-30 👌 IMPROVE: update README for CVserver
2024-05-30 📖 DOC: ESP32-CAM README add how to set WIFI credentials
2024-05-30 📖 DOC: add instructions about calibration to CVserver README
2024-05-31 invert x and y axis & remove commented code
    [sketch_webServer.ino]
2024-05-31 adapt to the new board
2024-05-31 use a very slow speed for calibration
2024-05-31 rename servo code folder
2024-05-31 feat(export): add "native" CAD assembly format
    [assembly.x_t]
2024-05-31 docs: change screws listed
2024-05-31 fix: small typo and missing screw part in README
2024-05-31 👌 IMPROVE: number detected buttons
2024-05-31 🐛 FIX: add access control headers to esp32-cam webserver
    [app_httpd.cpp]
